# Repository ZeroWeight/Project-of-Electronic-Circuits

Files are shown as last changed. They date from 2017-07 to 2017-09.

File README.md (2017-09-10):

# 电子设计小学期
## 整体工作
- Part 1
    - 在上位机控制下小车完成相关运动
    - 小车安装摄像头，将~~实时~~图像回传给上位机  
- Part 2  
    - 图像回传实时化
    - 小车完成相对位置信息的记录和回传
    - 利用位置信息进行
        - 二维地图的展示
        - 结合图像进行三维重建
- Part 3
    - 应用部署到移动平台
    - 小车安装避障自动运行

## TODOs（完成注明完成者）
- [x] 小车硬件部分 *ZeroWeight@20170830*
    - [x] 电源模块3V3，5，Webench上的开发工作 *ZeroWeight@20170823*
    - [x] PCB *ZeroWeight@20170823*
        - [x] ~~待校验~~ ~~有的焊盘不是特别稳定，需要不断调整~~不是不稳定，需要高级的焊接一发SMT *ZeroWeight@20170901*
    - [x] bts驱动调整 *ZeroWeight@20170830*
    - [x] 舵机调整，测试 *Archer@20170808*
    - [x] IMU，码盘等传感器安装和调试 *ZeroWeight@20170829*
- [x] FPGA部分（包含可能采用myRIO代替的工作） *Archer@20170905*
    - [x] 蓝牙信道的测试
        - 基于HC-05蓝牙转串口模块与上位机通信 ~~，有误码现象，需改进~~。*Archer@20170731*
    - [x] OV7670初始化和数据读取
        - `commit 9108e93` VCC3.3，SCL和SDA接4.7k上拉电阻，输出速度受串口限制。*Archer@20170804*
    - [x] IMU，码盘信息的采集和处理（可能使用myRIO主控） *ZeroWeight@20170905*
- [x] 上位机部分（包含可能的移动平台部署）*ZeroWeight@20170829*
    - [x] 蓝牙信道的测试
        - HC-05模块已设置为slave模式，上位机通过蓝牙连接后使用串口助手即可双向通信。*Archer@20170731*
    - [x] UI开发，整体架构 *ZeroWeight@20170805*
    - ~~[ ] 3D recon的处理~~
    - ~~[ ] 移动平台的部署~~
- [ ] 报告
    - [x] 预习报告 *ZeroWeight@20170827*
        - [x] 选题背景及课题简介 *ZeroWeight@20170825*
        - [x] 方案比较与选择（参考文献评述）*ZeroWeight@20170825*
        - [x] 基于FPGA的数字系统框图 *Archer@20170825*
        - [x] 传感器/执行机构接口电路图 *ZeroWeight@20170827*
        - [x] 基于Webench的电源电路仿真 *ZeroWeight@20170825*
    - [x] 选题展示PPT *Archer@20170827*
    - [x] 总结报告 *ZeroWeight@20170910*
        - [x] 课题开发与调试中出现的问题分析 *Archer&Zeroweight@20170909*
        - [x] 创新点（如有）*Archer&ZeroWeight@20170910*
        - [x] 附完整源码*ZeroWeight@20170909*
        - [x] 工作日志*ZeroWeight@20170909*
        - [x] 作品的视频 *Archer@20170908*
    - [x] 最终展示PPT *ZeroWeight@20170907*

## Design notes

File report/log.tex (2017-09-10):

\documentclass[a4paper]{paper}
\usepackage{ctex}
\usepackage{amsmath}
\usepackage{graphicx}
\usepackage{wrapfig}
\usepackage{multicol}
\usepackage{float}
\usepackage[colorlinks,linkcolor=black,anchorcolor=blue,citecolor=blue]{hyperref}
\title{
    \begin{large}电子技术课程设计\end{large}\\
    基于受控无人车的场地探测和3D重建系统\\
    项目详细日志
}
\author{
    张蔚桐\ 2015011493\ 自55\\
    陈　崴\ 2015011481\ 自55
}
\begin {document}
\maketitle

以下是整个项目的开发日志，代码开源托管在\href
{https://github.com/ZeroWeight/Project-of-Electronic-Circuits}{\underline{代码仓库}}上，这
里是开发过程中的commit记录。
其中各字符意义为\begin{itemize}\item [A]dd:增加文件/功能 \item[U]pdate：更新文件/功能 \item [D]elete:
删除文件/功能 \item [R]elease:发布功能进入稳定模式 \end{itemize}这里的项目日志删除了部分文件系统管理
日志，全部的提交记录请参阅\href{https://github.com/ZeroWeight/Project-of-Electronic-Circuits/commits/master}{\underline{提交记录}}\\ 
陈崴: [U] final commit @ Wed Sep 6 12:54:27\\ 
张蔚桐: [D] rm the useless mode @ Wed Sep 6 11:15:22\\ 
张蔚桐: Merge branch 'master' of github.com:ZeroWeight/Project-of-Electronic-Circuits @ Wed Sep 6 09:53:10\\ 
张蔚桐: [D] rm the labview file @ Wed Sep 6 09:09:28\\ 
陈崴: [A] ultrasonic ranging module @ Tue Sep 5 16:04:07\\ 
陈崴: Merge branch 'local' @ Tue Sep 5 14:55:59\\ 
陈崴: [U] not essential changes @ Tue Sep 5 14:55:41\\ 
陈崴: [U] servo and motor pwm @ Mon Sep 4 15:34:16\\ 
线上修改: Update README.md @ Sun Sep 3 19:34:21\\ 
线上修改: Update README.md @ Sun Sep 3 19:33:34\\ 
张蔚桐: [U] update Readme @ Fri Sep 1 08:40:03\\  
张蔚桐: [U] myRIO project resources @ Thu Aug 31 19:11:54\\ 
陈崴: [A] 7-segment nixietube display module @ Thu Aug 31 14:39:27\\  
张蔚桐: [U] now we can watch connan @ Wed Aug 30 12:51:53\\ 
陈崴: Ha. @ Wed Aug 30 12:39:16\\ 
陈崴: [D] debug @ Tue Aug 29 22:59:25\\ 
张蔚桐: [U] update ignore @ Tue Aug 29 00:25:02\\ 
张蔚桐: [U] Gyo finished @ Tue Aug 29 00:21:06\\ 
张蔚桐: [U] 1st day final host machine @ Mon Aug 28 16:51:38\\ 
张蔚桐: [U] release the host machine @ Mon Aug 28 15:26:18\\ 
张蔚桐: [A] add in myRIO ctrler @ Mon Aug 28 11:52:43\\ 
陈崴: [U] preview ppt @ Mon Aug 28 10:51:26\\ 
陈崴: [A] motor module @ Mon Aug 28 10:49:39\\ 
张蔚桐: [U] renew the host machine coder @ Mon Aug 28 09:25:54\\ 
张蔚桐: [U] recomplie the pdf file @ Sun Aug 27 12:36:37\\ 
陈崴: [U] preview ppt @ Sun Aug 27 11:41:34\\ 
陈崴: [U] fix typos @ Sun Aug 27 11:22:09\\  
陈崴: [A] preview ppt @ Sun Aug 27 11:06:43\\  
张蔚桐: [U] refine the preview report @ Sun Aug 27 10:47:07\\ 
线上修改: Update README.md @ Sun Aug 27 10:40:05\\ 
张蔚桐: [U] finish the preview report @ Sun Aug 27 10:37:57\\ 
张蔚桐: [U] typos and syntax errors fixed in preview report @ Fri Aug 25 18:11:54\\ 
陈崴: [U] report - fpga block @ Fri Aug 25 17:16:48\\ 
陈崴: [U] fpga block @ Fri Aug 25 17:15:56\\ 
陈崴: [U] gitignore @ Fri Aug 25 16:12:16\\  
陈崴: [U] report @ Fri Aug 25 16:01:43\\ 
张蔚桐: [U] webench simu finish @ Fri Aug 25 15:53:36\\ 
陈崴: Merge branch 'master' into local @ Fri Aug 25 14:55:42\\ 
陈崴: [A] FPGA block design @ Fri Aug 25 14:55:29\\ 
陈崴: [U] code indention @ Fri Aug 25 14:53:35\\ 
张蔚桐: [U] README“ @ Fri Aug 25 11:58:08\\ 
张蔚桐: [U] finish report 1 2 @ Fri Aug 25 11:56:54\\ 
张蔚桐: [U] report finish part 1 and 2 @ Fri Aug 25 11:45:14\\ 
线上修改: Update README.md @ Fri Aug 25 11:33:52\\ 
张蔚桐: [U] release PCB @ Thu Aug 24 09:17:36\\ 
陈崴: [U] try baudrate 115200 @ Wed Aug 23 22:35:12\\ 
线上修改: [U] Fin some awkward format errors on markdown @ Wed Aug 23 20:59:47\\ 
线上修改: Update README.md @ Wed Aug 23 20:56:35\\ 
线上修改: Update README.md @ Wed Aug 23 20:55:10\\ 
张蔚桐: [U] finish PCB @ Wed Aug 23 20:49:49\\ 
张蔚桐: [version update] static complie with Qt 5.9 @ Sun Aug 13 18:30:50\\ 
线上修改: Delete DesignRuleCheck.bak @ Fri Aug 11 10:39:47\\ 
线上修改: Delete Design Rule Check - PCB1.html @ Fri Aug 11 10:39:33\\ 
张蔚桐: [D] rm @ Thu Aug 10 09:27:49\\ 
张蔚桐: [U] rm the useless change @ Thu Aug 10 09:26:55\\ 
张蔚桐: [D] remove uesless PCB component @ Thu Aug 10 09:20:24\\ 
张蔚桐: [U] fix bugs of baudrate @ Thu Aug 10 09:15:10\\ 
线上修改: [U] servo @ Tue Aug 8 23:07:08\\ 
陈崴: [U] servo @ Tue Aug 8 22:59:28\\ 
陈崴: [A] servo @ Tue Aug 8 22:58:05\\ 
线上修改: [U] protocol - servo @ Tue Aug 8 22:03:54\\ 
张蔚桐: [A] add on protocol @ Tue Aug 8 10:55:48\\ 
张蔚桐: [A] pushbutton remote control finished @ Tue Aug 8 10:45:58\\ 
张蔚桐: [A] keyboard remote control finished @ Tue Aug 8 10:21:06\\ 
张蔚桐: [A] finish the PCB @ Mon Aug 7 21:00:14\\ 
张蔚桐: [U] update pins for OV @ Sun Aug 6 20:49:45\\ 
张蔚桐: [A] simply finish the PCB design @ Sun Aug 6 18:43:45\\ 
张蔚桐: [U] NOTE the host machine is release @ Sat Aug 5 11:59:01\\ 
张蔚桐: [U][R] Release the host machine - NOTICE     - You can run it in release mode     - Err ratio: approx 20%     - 1fps, but delay may exist     - do not care the free time of the seiral port     - NOTICE the command in /utility.cpp, LINE 82 @ Sat Aug 5 11:53:33\\ 
张蔚桐: [U]IMPORTANT UPDATE: fix bugs of host @ Sat Aug 5 11:27:21\\ 
张蔚桐: [U] temp commit with Graphics all white @ Sat Aug 5 11:13:19\\ 
张蔚桐: [U] temp commit with Graphics to fix @ Sat Aug 5 10:58:12\\ 
张蔚桐: [U] Temp update with bugs to fix @ Sat Aug 5 07:47:19\\ 
线上修改: [U] ov7670 @ Fri Aug 4 23:37:03\\ 
张蔚桐: [U] update host computer     - Greatly rely on performance of the computer     - Err ratio using demo: 1%     - Baud Rate: 1382400     - Without openGL or QImage @ Fri Aug 4 21:58:20\\ 
张蔚桐: [U] refine the structure of serial port @ Fri Aug 4 21:40:33\\ 
张蔚桐: [U] IMPORTANT UPDATE     - No data lost     - TODO: readALL()     - TODO: update the GL (or use QImage instead) @ Fri Aug 4 19:58:34\\ 
张蔚桐: [U] a temp commit with lots of bugs to be fixed @ Fri Aug 4 18:44:43\\ 
张蔚桐: [D] remove the baudrate controller @ Fri Aug 4 17:30:32\\ 
陈崴: [U] ov7670 @ Fri Aug 4 14:32:41\\ 
陈崴: [U] ov7670 works well @ Fri Aug 4 14:25:36\\ 
线上修改: [U] fix @ Fri Aug 4 12:56:41\\  
陈崴: Merge branch 'local' @ Fri Aug 4 12:48:31\\ 
陈崴: [U] ov7670 generally works: 修改了一下初始化配置，不一定比原来好，可以进一步测试。现在初始化返回值共517字节。初始化后的几帧可能不太稳定，直接舍弃。 读取图像速度改为100us每字节，需在上位机方面优化。图像可能出现某块状或条状区域数据异常，表现为彩块或彩条。 @ Fri Aug 4 12:30:52\\ 
张蔚桐: [U] update the BOM @ Thu Aug 3 22:03:29\\ 
张蔚桐: [A] resource of PCB all finished @ Thu Aug 3 18:16:16\\ 
陈崴: Merge branch 'master' into local @ Thu Aug 3 18:13:04\\ 
张蔚桐: [bug fixed]     - fix the bug of exit     - refine the method to write to files     - can accept 10ms/640B input     - may rely on the performance of computer     - NOT stable @ Thu Aug 3 16:59:16\\ 
张蔚桐: [U] output to file, BUG: cant exit normally @ Thu Aug 3 12:39:47\\ 
陈崴: [D] x64/Release/UserInterface.exe @ Thu Aug 3 09:41:27\\ 
陈崴: [U] read frame data (simply tested) 	- 摄像头只可初始化一次，若初始化中断或错误或重新初始化，则需要重新上电。所以注释了OV\_INIT.v LINE51。 	- （未测试）目前只处理了QVGA的一帧，即只使用FIFO的一半空间。 	- 目前发给上位机的数据中，前328B为初始化返回值，若初始化成功，则第7字节为0x73，第11字节为0x76，第327字节为0x0D，第328字节为0x0A，其余字节为0x00。 	- （未测试）从第329字节起为图像数据，前320×240×2字节为RGB565数据，最后2字节为0x0D、0x0A。似乎数据仍有错误，需要进一步测试。 	- 目前发送图像数据的逻辑为：当FIFO中写满了一帧QVGA数据，OV\_READ模块按字节传给顶层，两字节间隔10us；顶层每接收到一个字节，立即以波特率115200发给上位机。 @ Thu Aug 3 00:32:17\\  
陈崴: [U] ov7670 initialization @ Wed Aug 2 21:54:40\\ 
张蔚桐: [A] Bill Of Materials @ Wed Aug 2 15:45:23\\  
线上修改: [U] low level indicates success @ Wed Aug 2 15:04:56\\ 
张蔚桐: [U] clear queue when establishing the connect @ Wed Aug 2 09:14:29\\ 
张蔚桐: [U] upper demo @ Wed Aug 2 09:12:25\\  
张蔚桐: [A] release project to .exe @ Tue Aug 1 20:15:35\\ 
陈崴: [U] fix LINE144 @ Tue Aug 1 20:00:55\\ 
张蔚桐: [U] bug fixed and finish the verify of the image @ Tue Aug 1 19:51:46\\ 
线上修改: [U] fix LINE144 @ Tue Aug 1 19:49:58\\ 
张蔚桐: [U] Finish Serial Port connection @ Tue Aug 1 19:08:30\\ 
陈崴: [A] rtl top (untested) 	整合了摄像头初始化、数据读取和串口通信。 	帧数据按每像素先高字节后低字节的顺序发送至上位机，每帧以0x0D 0x0A结束，共320 × 240 × 2 + 2 = 153602字节。 @ Tue Aug 1 18:28:01\\ 
陈崴: [U] ov7670 initial configuration 	QVGA RGB565 @ Tue Aug 1 18:26:17\\ 
陈崴: [A] read frame data (untested) @ Tue Aug 1 15:09:45\\ 
张蔚桐: [U] preview report section 2 finished @ Tue Aug 1 11:00:10\\ 
张蔚桐: [D] remove useless project in circuit/ @ Tue Aug 1 09:00:58\\ 
线上修改:  [A] sccb interface (untested) @ Mon Jul 31 23:16:26\\ 
陈崴: [U] ov7670 initial configuration @ Mon Jul 31 22:30:30\\ 
陈崴: [A] sccb interface (untested) @ Mon Jul 31 21:32:49\\ 
线上修改: [A] uart modules @ Mon Jul 31 20:08:05\\ 
张蔚桐: [D] del some unuseful qss file @ Mon Jul 31 19:47:15\\ 
张蔚桐: [R] UI basically finished @ Mon Jul 31 18:42:03\\ 
陈崴: [U] bluetooth communication @ Mon Jul 31 16:32:17\\ 
陈崴: [A] uart modules 	Verilog串口模块，波特率可调，8数据位，无校验位，1停止位。 	高波特率时有误码现象，需改进。 @ Mon Jul 31 16:14:46\\ 
张蔚桐: [A] user interface @ Mon Jul 31 11:56:44\\ 
张蔚桐: [F] 3v3 sch finished @ Sun Jul 30 19:50:00\\ 
张蔚桐: [A] PCB lib for AD add in, @ Sun Jul 30 19:08:30\\ 
张蔚桐: [U] report tasks @ Sun Jul 30 11:25:30\\ 
张蔚桐: [A] blank task table finished @ Sun Jul 30 11:16:58\\ 
线上修改: Update README.md @ Sun Jul 30 11:09:12\\ 
张蔚桐: [A] Readme @ Sun Jul 30 11:03:05\\ 
张蔚桐: [A] README @ Sun Jul 30 11:01:59\\ 
张蔚桐: [A] CHN datasheet and SCCB code @ Sat Jul 29 15:59:44\\ 
张蔚桐: [A] OV datasheet and summary @ Sat Jul 29 12:05:27\\ 
张蔚桐: Initial commit @ Sun Jul 9 09:31:41\\ 
\end{document}

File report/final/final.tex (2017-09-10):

% compile with xelatex
\documentclass[a4paper]{paper}
\usepackage{amsmath}
\usepackage{ctex}
\usepackage{diagbox}
\usepackage{float}
\usepackage{graphicx}
\usepackage{multirow}
\usepackage{multicol}
\usepackage{rotating}
\usepackage{wrapfig}
\usepackage[colorlinks,linkcolor=black,anchorcolor=blue,citecolor=blue]{hyperref}
\newcommand{\tabincell}[2]{\begin{tabular}{@{}#1@{}}#2\end{tabular}}
\title{
    \begin{large}电子技术课程设计\end{large}\\
    基于受控无人车的场地探测和3D重建系统\\
    终结报告
}
\author{
    张蔚桐\ 2015011493\ 自55\\
    陈　崴\ 2015011481\ 自55
}
\begin{document}
\maketitle
\tableofcontents    
\clearpage
\section{选题背景及课题简介}
根据《智能交通》和《智能家居》的课题方向，我们将选题定位为基于受控无人车的场地探测和3D重建系统。

\begin{wrapfigure}{r}{0pt}
    \centering
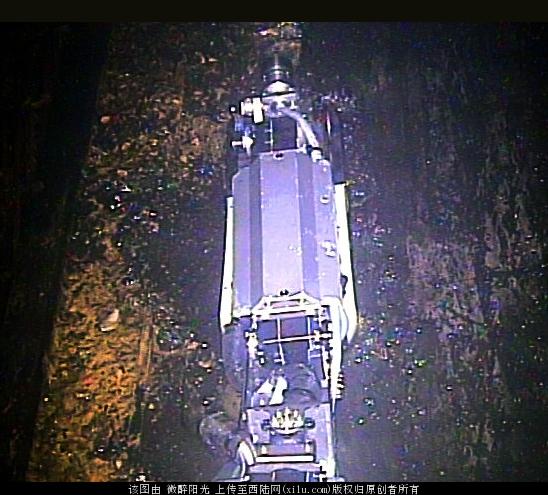
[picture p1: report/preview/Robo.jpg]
    
    \caption{“蝎形”（"scorpion"）机器人行进在福岛核电站2号反应堆内}
    \label{Robo}
\end{wrapfigure}
目前，受控无人车，即对无人车发送指令控制无人车的技术已经有了很多现实生活中的应用。然而，
这种受控无人车要求控制者能够看到无人车的运动状态，并对无人车进行控制。这样不方便无人车进一步
进行无人作业。例如，在地震灾区倒塌的房间中，控制人员无法看到无人车的具体位置，这就需要无人车
对周边环境数据进行采集，方便控制人员进行进一步的控制。另外，通过加装场地检测装置，无人车或
机器人可以到很多危险场合进行作业和信息的采集。例如，2011年日本福岛核泄漏之后，东电公司曾派遣如图
\ref{Robo}所示的机器人到反应堆内调查事故情况。通过加装摄像头和辐射监测设备，机器人可以在人类
无法承受的辐射量内进行高强度监测作业。

另外，目前3D检测和建模技术方兴未艾。利用无人机等设备对建筑物外表面进行3D检测建模的技术已经实现。
计算机视觉领域内，SfM(Shape from Motion)等基于单目摄像机的3D重建技术已经相对比较成熟，因此，
周边技术的成熟为我们的设计提供了相当的基础。同时，我们也考虑采集小车的位置信息，一方面，
对于控制人员来说，了解小车的行进路线（相对位置）也是一个很重要的信息点，另外一方面，根据计算机
的相关知识，我们也可以知道获取准确的拍摄角度和拍摄位置可以更好的加大3D重建的精度，而这方面的应用和算法
据我们所查阅的资料来看相对较少，可以进行进一步的创新。

因此我们将选题定位基于受控无人车的场地探测和3D重建系统，目标是通过控制无人车的行为，完成对场地内
图像信息的采集，并在合适的情况下允许上位机进行3D重建，完成对场景3D状态的描述工作。根据时间限制
和具体的完成情况，我们将整个项目分为如下几个部分进行。
\begin{enumerate}
    \item 第一部分
    \begin{itemize}
        \item 基本的电源管理和小车运动控制
        \item 在上位机控制下小车完成相关运动
        \item 小车安装摄像头，将图像回传上位机
    \end{itemize}
    \item 第二部分
    \begin{itemize}
        \item 图像实时回传
        \item 小车完成相对位置信息的记录和回传
        \item 利用位置信息进行二维地图的展示工作
    \end{itemize}
    \item 第三部分
    \begin{itemize}
        \item 将上位机应用部署到移动平台
        \item 小车安装避障系统，并可以自动运行
        \item 三维重建，同时利用位置信息
    \end{itemize}
\end{enumerate}
从上面我们可以看出整个工程量较大，受到两周的开发时间的限制可能不一定全部完成，剩余工程可以
作为参加挑战杯等进一步开发项目的发展方向。
\subsection{具体完成情况}
这一节总结一下提到的项目内容的完成情况

经过两周的具体调试，我们实现了第一部分的所有具体要求，包括小车的驱动模块，摄像头的安装和
测试，蓝牙模块通信的测试等，并完成了整个项目的整合。但是由于蓝牙速度较慢，经过了长时间的
调试，我们仍然不能实现图像的实时回传，同时，由于图像数据量较大，回传图像对蓝牙压力也比较大
导致蓝牙模块并不是很稳定。虽然如此，整个项目的工作量，完成度和可展示性还是非常理想的，尤其是
对基于FPGA对裸CMOS摄像头OV7670的封装等为代表的工作花费了我们大量的心血，总结起来还是比较满意的。
\section{方案比较与选择}
\subsection{主控元件的选择}
首先我们考虑主控元件的选择，根据我们的技术水平和课题的情况，可供选择的主控芯片为MCU
（单片机）和FPGA。相比FPGA，MCU具有开发相对简单的优势，以串口通信协议为例，大部分MCU
的系统库中均已经封装了串口通信协议，而FPGA相对更接近底层，因此需要自行完成相关的通信协议
的封装，这将消耗大量的时间和精力。

然而，相比于MCU，FPGA在速度和并行性方面有着很大的优势。根据我们查阅的资料，以STMF103为例，
其时钟速度可以达到72MHz，然而由于串行执行的原因，IO速度相对于FPGA较低；对比我们使用的Xilinx
FPGA，其时钟速度可以达到100MHz，同时高度并行使得模块之间互相不干扰，保证了IO速度等要求。

因此，考虑到性能要求以及课程需要，我们在硬件方面采用了FPGA作为主控进行开发。
\subsection{通信机制的选择}
根据查阅的资料，可供选择的无线通信机制有如下三种：

\begin{enumerate}
    \item WiFi信道

    这种通信机制需要将WiFi模块植入硬件，使得小车可以联网传输信息。
    上位机或移动平台使用WiFi下载信息。这种方式的优势一方面是信息传输距离较远，
    在一个路由器覆盖的范围内，信息均可以被传输。另一方面可拓展性也比较强，
    如果设计了合理的联网方式，将进一步解除距离限制，通过将信息上传到云空间，
    用户可以在任何联网的地区完成信息的收取和对小车的控制。

    这种通信机制的缺点是过于复杂，尤其是使用FPGA进行开发的情况下，网络通信协议
    将带来更大的开发时间消耗，不适用于本课程的短期开发。

    \item 蓝牙信道

    这种通信机制利用蓝牙模块，蓝牙模块已经将蓝牙信道封装成串口的形式，
    从很大程度上方便了开发。同时，通过对电脑，移动设备上的蓝牙模块进行开发，
    用户可以不依赖于第三方设备（如路由器）和小车进行通信。虽然通信速度上相比WiFi也
    有一定的损失，并且通信距离受到明显限制，但相比于WiFi模块而言，其功耗更小。

    \item SPI信道

    后期的开发表明，蓝牙的速度并不能保证摄像头传输的实时性，因此后期考虑采用SPI信道
    替代原有的蓝牙信道，然而相比于蓝牙——串口信道，SPI的开发不论是在上位机方面还是在
    FPGA方面均比较复杂，因此不一定可以完成。

\end{enumerate}
综合以上三种通信机制的优缺点，我们选择蓝牙信道作为通信手段。
\subsection{供电方式的选择}
首先通过查阅可能使用到的外设的技术手册，我们大概确定了供电需求为
\begin{itemize}
    \item 5V@1.5A
    \item 3.3V@1.5A
    \item 7.2V@40A
\end{itemize}
其中5V@1.5A负责向FPGA 5V@1A以及舵机供电，3.3V电源负责向外设供电，例如我们采用的摄像头OV7670
采用的供电电压为3.3V@100mA。7.2V@40A电源负责向电机供电，并应接受PWM调制来控制电机转速。

通过查阅资料我们发现，供电的难点在7.2V@40A电源，而5V@1.5A电源和3.3V@1.5A电源
均可以使用实验室提供的TPS54160 SMT芯片完成设计，
这一部分内容将在后面基于Webench的仿真实现上面进行说明。7.2V@40A电源的电流限额主要受到电机供电电流要求
影响，从实验室提供的数据手册我们可以发现，电机的空载电流2.4A，最高效率电流11A，堵转电流52.8A，根据网上
查阅的相关资料，电机的限流应当是最高效率电流的约4倍，因此设计7.2V@40A电源负责向电机供电。

这里讨论7.2V@40A电源的设计问题。因为需要接受PWM信号调制，因此我们采用了H桥进行设计。
\begin{wrapfigure}{r}{0pt}
    \centering
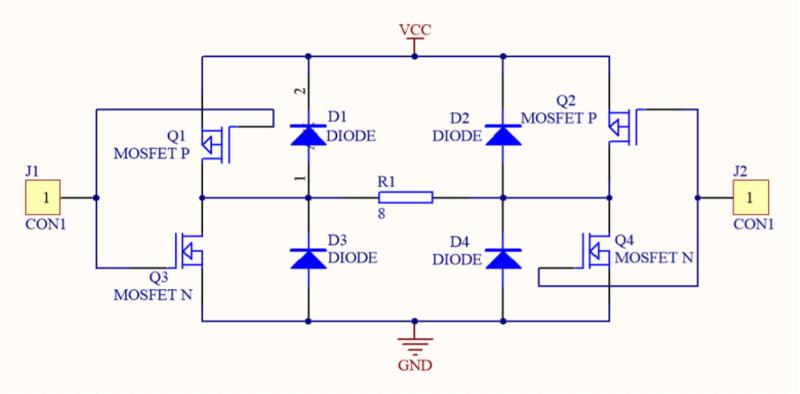
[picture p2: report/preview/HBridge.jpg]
    
    \caption{H桥的电路原理图}
    \label{H-bridge}
\end{wrapfigure}
H桥的电路原理图如图\ref{H-bridge}所示。Q1\~Q4可以由处于饱和状态的三极管或开关状态的MOS管组成 
J1 和 J2 分别接入前一级驱动电路产生的两个反相PWM，设某时刻 J1 为高电平，
则 Q3 导通，Q1 截止；由于反相，J2 为低电平，Q2 导通，Q4 截止，
电流由通过 Q2，经负载，再经过 Q3 流入地。
同理，当某时刻 J1 为低电平时，Q1,Q4 导通， Q2,Q3 截止，
电流依次经 Q1,R1,Q4 流入地。综上，任意时刻有且只有一个对角线上的两个MOS管是导通的。

对于电机，我们可以设定刹车模式，即可以通过与上述方法类似的方法将电机两脚短路，使得电机
迅速产生电磁制动实现刹车效果

通过搜索符合要求的元件，我们发现合理的解决方案为bts7960/7961芯片和自行搭建H桥两种方案。

bts7960/7961芯片是接受5VPWM信号调制的，输入电压5.5V至27V@43A的半H桥电路，
采用SMT封装，输出电流符合要求。
然而，由于我们电机的额定输入电压为7.2V，经过对电机的初步调试我们可以发现
电机在7.2V输入电压下的转速非常高，导致速度不能得到控制，
经过进一步的实验我们发现，在低于数据手册上提供的5.4V供电的情况下，
电机的转速可以保证一个理想的状态，因此可以初步得到结论即PWM信号的占空比不可过高。

而自行搭建H桥，因为工艺比较复杂，同时在网上找不到合适的大功率MOS管供应商，
因此我们放弃了这个方案。

\subsection{摄像头数据传输技术的选择}
我们采用的OV7670摄像头，可以输出25fps 640*480 VGA格式的RGB三色图像，输出采用8线同步并行传送
因此输出时钟速度可以达到$25*640*480 \approx 8\mathrm{MHz}$。
收到蓝牙信道是串行接口的原因，蓝牙信道的速度必须达到8MB/s，这是一般蓝牙系统很难做到的。
因此不论是FPGA读取信息还是蓝牙传输信息的速度，均不如摄像头采集数据的速度，需要找到合理的解决方式。

经过我们查阅相关资料发现，OV7670的传输方式有如下三种形式：
\begin{wrapfigure}{r}{0pt}
        \centering
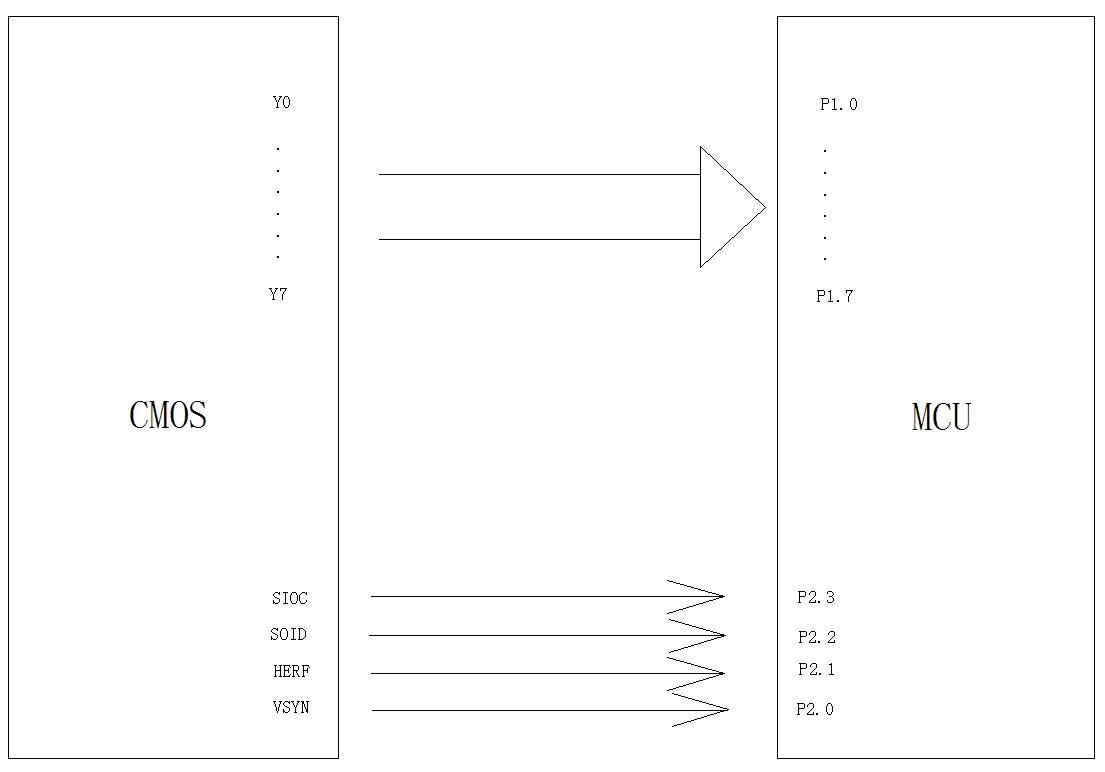
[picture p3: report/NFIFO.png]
        
        \caption{MCU/FPGA直接采集}
        \label{fig2}
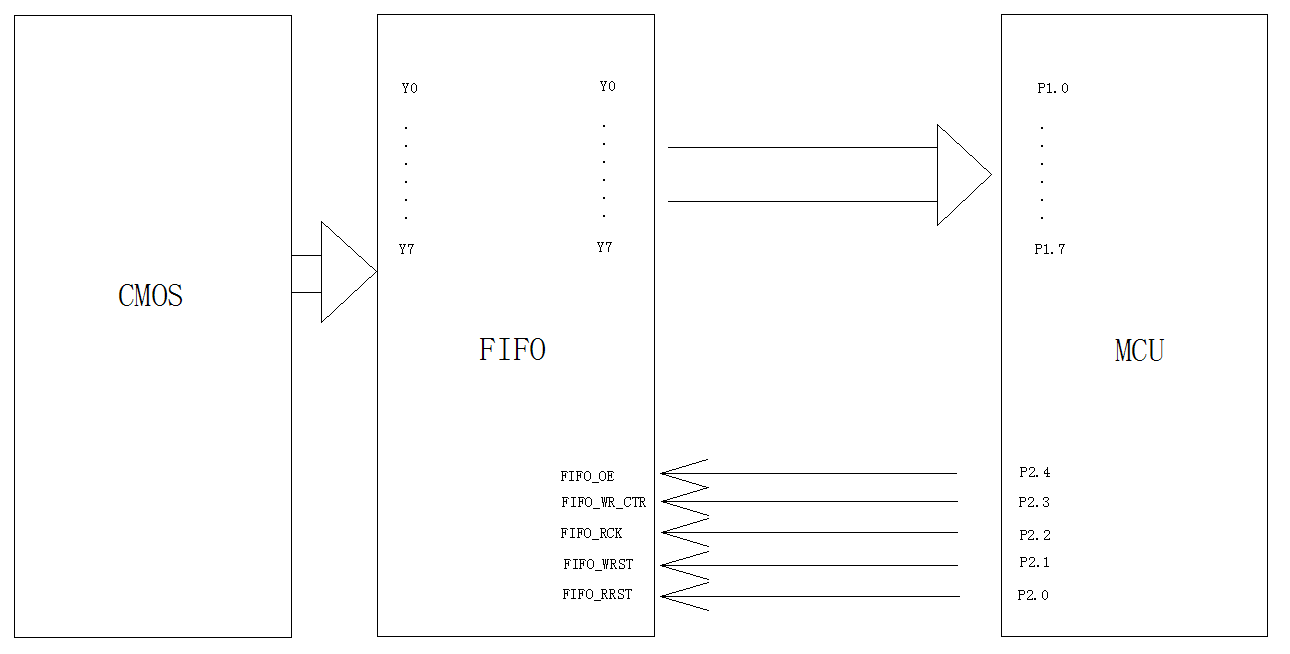
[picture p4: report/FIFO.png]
        
        \caption{FIFO采集}
        \label{fig3}
\end{wrapfigure}
\begin{itemize}
    \item MCU/FPGA直接采集：

    如图\ref{fig2}所示，这种方法是最简单，最直接，但也是最不好实现的方法，
    以MCU为例，多数的CMOS 芯片（如OV7670）的时钟速度可高达24M，
    一般MCU的IO 端口速度根本不可能达到，所以需要高速MCU。
    这对多数用户来讲有些不现实。但也不是完全没有办法在低速上实现采集，
    方法也很简单，那么就是降低CMOS的输出速度，
    不过这需要靠外部的晶振和内部的PLL电路以及像素时钟速度，
    帧速等多个寄存器共同设置，并且要和MCU的IO速度匹配才可实现。
    但这么做将带来巨大的寄存器设置工作量并导致硬件图像的采集速度
    可能下降到0.5帧以下，同时带来图像失真的可能。
\end{itemize} 

\begin{itemize}
    \item DMA方式

    这种方式主要用于MCU中，FPGA中这种方式效果不明显，DMA控制器使得数据
    可以绕过CPU直接进入内存，但是在FPGA中，同时受到串口通信速度的影响，
    这种方式效果也不是很明显。

    \item FIFO模块采集

    如图\ref{fig3}，用户只需要按上述时序图控制相关的几个控制引脚即可，可以很
    方便的使用在低速MCU上，另外一个好处是，可以直接IO口读取数据，
    读出的数据可以直接送屏，也可以经过MCU简单处理；当然也可以不经过
    MCU，直接送到屏等外围器件使用。对于FPGA，以及速度相对较低的串口单元，
    使用FIFO也能很大程度的解决速度不同步的问题。

\end{itemize}
\subsection{车辆位置角度信息处理方式的选择}
为了进一步增强3D建模的精度，我们希望能够采集车辆的位置信息和角度信息。
由于摄像头和车辆是相对固定的，这样也就获得了摄像头的位置信息和角度信息。

根据我们查阅到的资料，车辆的位置信息和角度信息有几种不同的获取方式，如下所示。
\begin{itemize}
    \item 惯性测量单元（IMU）模块

    通过加速度计和陀螺仪的信息，可以直接读取车辆的加速度和角度。
    经过积分之后可以得到车辆的速度信息和角度信息，这种方法最简单，
    但是误差最大，加速度计易受到颠簸，碰撞，刹车等造成的脉冲影响，
    并进一步影响积分的准确性。角速度计（陀螺仪）具有一般性的零点迁移
    问题，这包括动态的零点波动和静态的温漂。经过积分会导致角度信息
    相当不准确。这种方法只能作为一种简单的参考，实用时必须加以处理。

    \item 磁场计

    通过对地磁角度的测定，可以直接获取车辆的角度，并通过加速度计等
    方式获得车辆的速度，这种方式误差相对前一种较小，
    但是受外界磁场的影响比较严重，尤其是当存在10A绕组的电机驱动时，
    这种方法可以认为无效。

    \item 码盘

    这种方法通过测量车辆四轮的转速经过解算得到车辆的具体位置，相比于
    之前几种方式，这种方式依赖于更加准确的光电传感器，因此得到的值也
    相对比较准确，这种方法的难点在于必须对车辆的刚性模型进行建模，
    同时安装码盘也是一个硬件上的难点。
\end{itemize}
综合提到的几种方法，我们计划采取IMU+信号处理+码盘解算几种方式
得到车辆的具体位置，希望通过反馈等方式希望得到更准确的车辆控制。

\subsection{其他注意事项}
在设计对车辆相对位置进行测量的过程中，考虑到FPGA在解算浮点数方面比较难以开发，
我们选用了NI myRIO进行解算和控制，并采用myRIO自带的WiFi进行相关数据的回传。

NI myRIO是NI针对教学和学生创新应用而最新推出的嵌入式系统开发平台。
NI myRIO内嵌Xilinx Zynq芯片，使学生可以利用双核ARM Cortex-A9的
实时性能以及Xilinx FPGA可定制化I/O，学习从简单嵌入式系统开发到
具有一定复杂度的系统设计，采用LabView语言进行可视化编程。
通过myRIO可以大幅简化控制算法如PID的调试过程，显著降低开发难度，加速开发进度。
\subsection{实际项目的修正和改动}
实际项目进行过程中，我们尽可能的对蓝牙的速度进行了利用，然而由于蓝牙速度受限，
导致实际上图像回传不能实时化，并且对蓝牙通信速度上限的冲击导致蓝牙出现不稳定情况。
在这种情况下，我们希望采用SPI-WiFi-TCP通信协议，然而TCP协议封装复杂，
经过我们查阅相关资料，TCP的引脚数量甚至超过了我们使用的FPGA的全部可控引脚数量，‘
同时TCP通信机制也比较复杂，会对是FPGA层面的封装还是上位机的编写带来巨大的困难，
因此我们最终放弃了这种思路。

同时，对于陀螺仪和测速方面，由于我们使用的FPGA引脚已经全部被占用，导致基于FPGA
的相关开发变得不现实，因此我们选用了NI myRIO进行相关的开发，并完成了陀螺仪模块。
对于测速模块，我们发现不论是车轮还是电机均很难安装码盘，因此我们采用了对车轮进行
标注并利用红外进行测速，并基于myRIO调通了相关的功能，然而由于我们设计的车辆行驶
速度偏慢，因此相关的测速变得没有实际意义，最终我们放弃了这个模块的整合工作。
\section{基于FPGA的数字系统框图}
\begin{figure}
    \centering
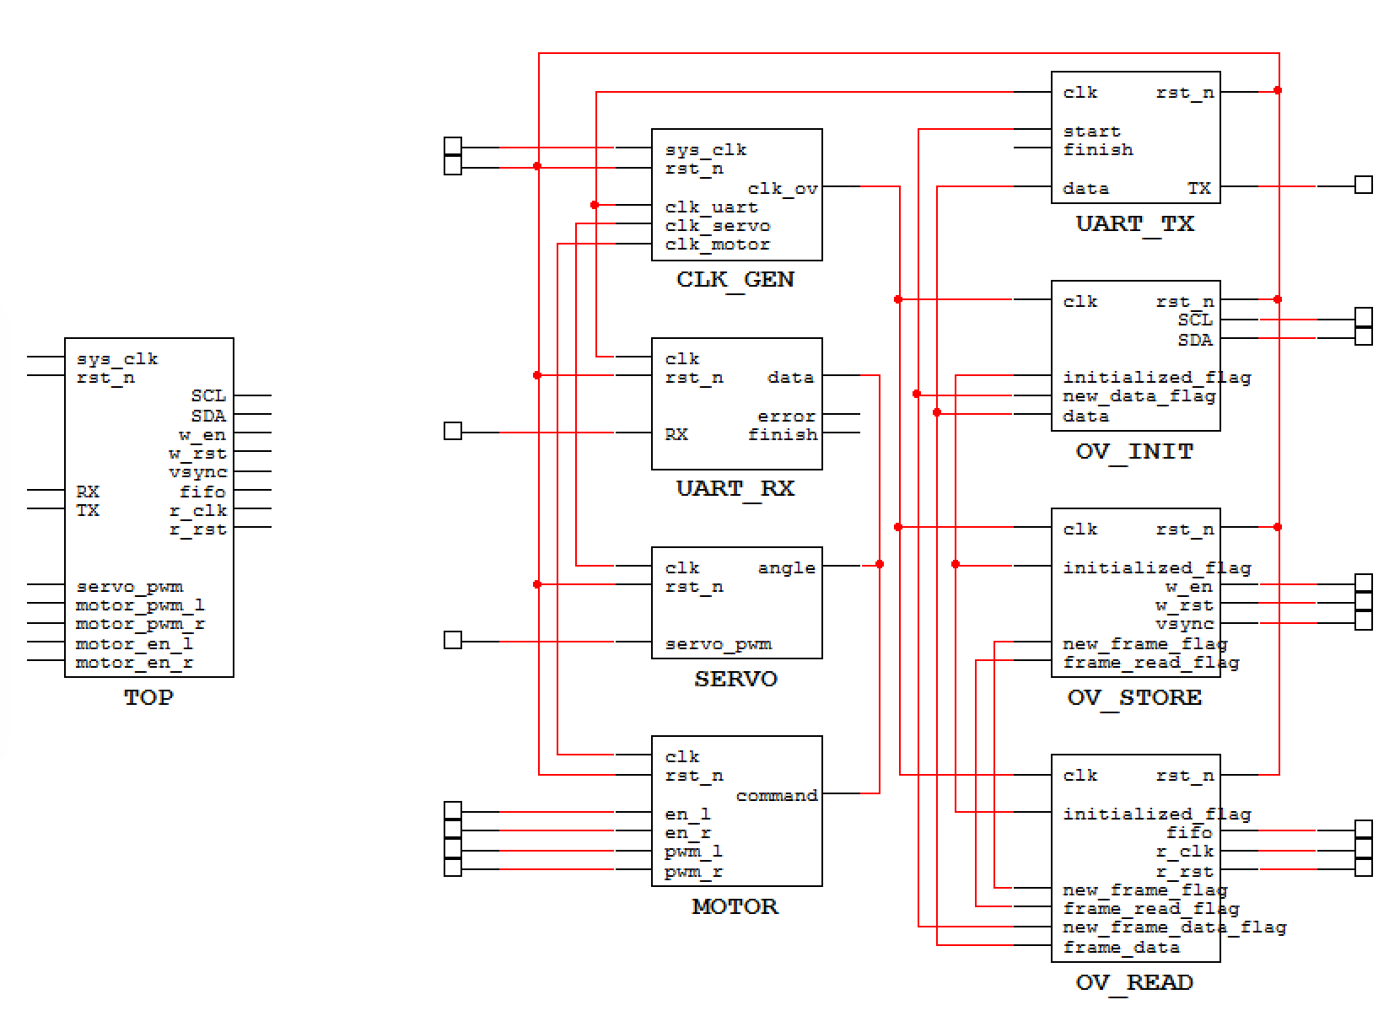
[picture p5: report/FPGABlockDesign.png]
    
    \caption{基于FPGA的数字系统框图}
    \label{FPGABlockDesign}
\end{figure}
如图\ref{FPGABlockDesign}所示，左侧为封装的顶层模块，从右侧可以看出共分为8个子模块。
\begin{itemize}
    \item CLK\_GEN

    该模块对100MHz系统时钟分频，输出4个时钟分别供串口、舵机、电机、摄像头使用。

    \item UART\_RX

    蓝牙串口接收模块，RX为数据线，每从上位机接收一个码元即触发finish信号，并将数据存
    在data寄存器供其他模块使用。同时内部还提供了一个error接口，接收数据发生错误时触发。

    \item UART\_TX

    蓝牙串口发送模块，TX为数据线，当触发start信号后，将data寄存器中的内容发送给上位机，
    发送完成后会得到一个finish信号反馈。

    \item SERVO

    舵机控制模块，从串口接收转向控制指令，输出舵机PWM信号。

    \item MOTOR

    电机控制模块，同样从串口接收指令，输出电机使能和PWM信号。

    \item OV\_INIT

    摄像头初始化模块，SCL和SDA为SCCB协议的时钟线和数据线，初始化前initialized\_flag为
    低电平，OV\_STORE和OV\_READ处于失能状态，初始化完成后拉高initialized\_flag，摄像头
    便可正常工作。

    \item OV\_STORE

    将摄像头采集到的图像存储于FIFO中，存储完成一帧后触发new\_frame\_flag信号，等待FPGA
    读取图像结束后才继续采集下一帧。

    \item OV\_READ

    从FIFO中读取一帧图像，并存储在frame\_data寄存器中，读取完成后触发两个信号，一个是
    frame\_read\_flag，通知摄像头可以继续采集下一帧图像，另一个是new\_frame\_data\_flag，
    通知顶层模块将读取到的数据发送给上位机。
    
\end{itemize}
\section{传感器/执行机构接口电路图}
\subsection{传感器电路}
\subsubsection{数字接口电路}
\begin{wrapfigure}{r}{0pt}
    \centering
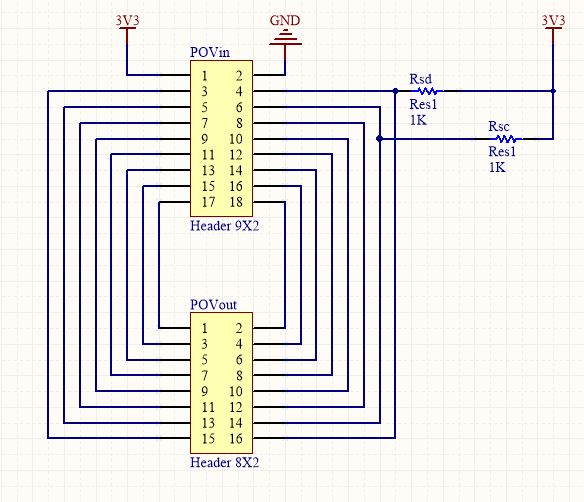
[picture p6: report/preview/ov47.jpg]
    
    \caption{OV上拉电阻和转接电路}
    \label{OV}
\end{wrapfigure}
这部分主要是完成数字模块之间的接口电路，由于各个数字模块已经将输出电平统一标准化为TTL电平，
因此这部分的关键主要是接口通信协议的实现，主要有FPGA方面实现了SCCB接口通信协议，串口通信协议，
摄像头数据读取协议等。另外，SIO\_C和SIO\_D分别为SCCB总线的时钟线和数据线，为了
方面对多个设备进行控制，OV的SCCB两个端口采用的均是OC门输出，需要上拉4.7k
电阻实现输出高低电平，这些需要在设计PCB的时候尽可能的考虑到并保证接线的
稳定性和摄像头位置的稳定性，因此需要在PCB上统一制作并提供对FPGA的简单的接线电路，这部分的电路
可以如图\ref{OV}所示。

\begin{wrapfigure}{r}{0pt}
    \centering
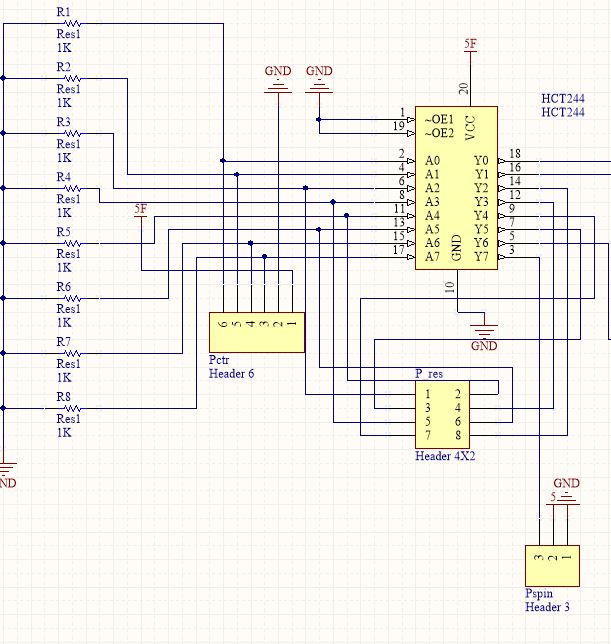
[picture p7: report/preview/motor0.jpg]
    
    \caption{74HC244驱动器电路}
    \label{motor0}
\end{wrapfigure}
另一部分的接口电路问题是3.3V电平标准和5V电平不匹配的问题以及同时设计到的FPGA驱动能力不足的问题
通过查阅给定的技术手册我们发现FPGA输入电流1A，标准的输出电压为3.3V，
而不论是电机驱动的PWM还是舵机驱动的PWM均为5V，这中间需要设计适当的接口
电路，同时，由于工程量比较大，担心FPGA会出现总线电流过大或无法驱动相关
接口电路的情况，因此我们采用了74HC244芯片作为接口的辅助电路，74HC244是
一款高速CMOS驱动芯片，支持三态门使能，通过HC244我们可以顺利的将3.3V输出转化为5V，
并提升驱动能力。根据74HC244的接线要求，我们在输入端接入下拉电阻1k实现相关功能。这部分的电路
有如图\ref{motor0}所示。同时我们将剩下的74HC244引脚同样通过排针引出，留待之后使用。

\subsubsection{模拟接口电路}
\begin{wrapfigure}{r}{0pt}
    \centering
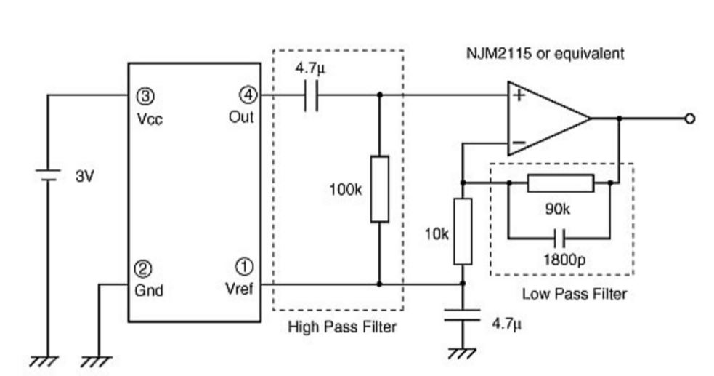
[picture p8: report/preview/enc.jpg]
    
    \caption{ENC-03模块外部电路图}
    \label{ENC}
\end{wrapfigure}
我们计划采用输出模拟电压的ENC-03陀螺仪，这是是一种应用科氏力原理的角速度传感器，
陀螺输出一个和角速度成正比的模拟电压信号。通过积分电路可以得到相关的角度等。根据ENC-03
技术手册，我们设计输出放大电路如图\ref{ENC}所示，整个电路由两个滤波器组成，左侧为低通滤波器，
用于滤除传感器高频噪声，右侧为高通滤波-放大电路，用于放大电压信号和滤除低频温漂。

进一步，我们搭建基本积分电路可以得到角度信息，两个信息通过AD模块可以返回给主控设备。
由于我们计划采用myRIO进行位置信息的测量，因此这部分可以直接使用LabVIEW语言在myRIO上完成，
就没有设计电路的必要了。

\subsection{执行接口电路}
这部分主要描述的是对电机和舵机的驱动电路

对于舵机驱动，单片机输出高电平为3.3V的PWM脉冲，经过前文提到过的74HC模块转5V驱动舵机旋转。

\begin{wrapfigure}{r}{0pt}
    \centering
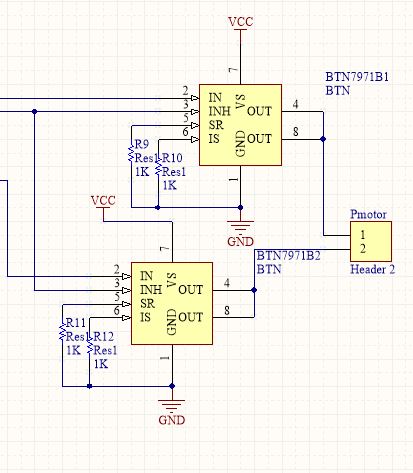
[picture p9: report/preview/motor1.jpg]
    
    \caption{电机驱动电路}
    \label{motor1}
\end{wrapfigure}
对于电机驱动，我们使用BTN7970模块，如图\ref{motor1}所示。这里为了方便后文叙述，两片IN引脚被
命名为IN1，IN2，两片INT引脚被命名为INT1,INT2。我们将INT1,INT2短接并输入PWM波形控制电机转动速度。
将IN1，IN2分别接高低电平控制电机正转反转。例如\{INT1 = 0,INT2 = 1\}代表电机正转，\{INT1 = 1,
INT2 = 0\}代表电机反转。当\{INT1 = 0,INT2 = 0\}时，H桥全部关断，表示不控制电机转动。
当\{INT1 = 1,INT2 = 1\}时，H桥下部导通，电机两端短接，使得电机的机械能通过电磁感应和短路线
迅速释放，实现刹车功能。BTN相关引脚仍为5V接线，因此使用74HC244完成相关的电平转换和放大工作。
\section{基于Webench的电源电路仿真}
WEBENCH是TI公司提供的设计环境，通过软件工具提供定制电源等的设计，通过使用WEBENCH可以
提升设计效率。整体的设计思路如下：
\begin{itemize}
    \item 输入电压的确定

    我们将电池断开，测量电压约为8.2V，将电池直接接电机，并在电机上施加比较大的阻力，发现
    电源电压约为7V，因此我们设计电源时考虑输入电压为6V\~9V即可满足需求。

    \item 输出电压的确定

    由表\ref{t1}所示，我们需要向FPGA提供5V外接电源，对舵机提供5V外接电源，
    对外设提供3.3V外接电源，因此设计输出电压为5V，3.3V。

    \item 输出电流的确定

    首先根据实验室提供的TI样片，我们选择了TI TPS54160降压模块，TPS54160器件是一款带有集成型
    高侧MOSFET的60V,1.5A的降压稳压器。电流模式控制提供了简单外部补偿和灵活组件选择，功耗较小。

    根据TPS54160的输出电流，我们限制电源输出电流为1.5A。同时查阅技术手册可以得到主要的部件
    的供电信息如表\ref{t1}所示,总计需要输出电流5V@2A,3.3V@500mA，因此需要设计两路5V供电电源，
    其中一路FPGA自用（包括驱动器74HC244），一路给舵机/外设使用。

\end{itemize}
因此，进入WEBENCH中提供需求的输入，输出信息，选择器件为TPS54160，可以得到元件的原理图。
通过调整原理图上的元件的值的信息，可以选用已有阻值的元件进行仿真，最终确定的电路原理图和
响应时间仿真和稳态仿真如下面几张图所示。两个电路结构相同，相关参数差别如表\ref{t2}所示。
整理仿真结果如表\ref{t3}所示。可以看出电源的性能效果还是比较理想的，可以进行实际电路的搭建。
\begin{figure}
    \centering
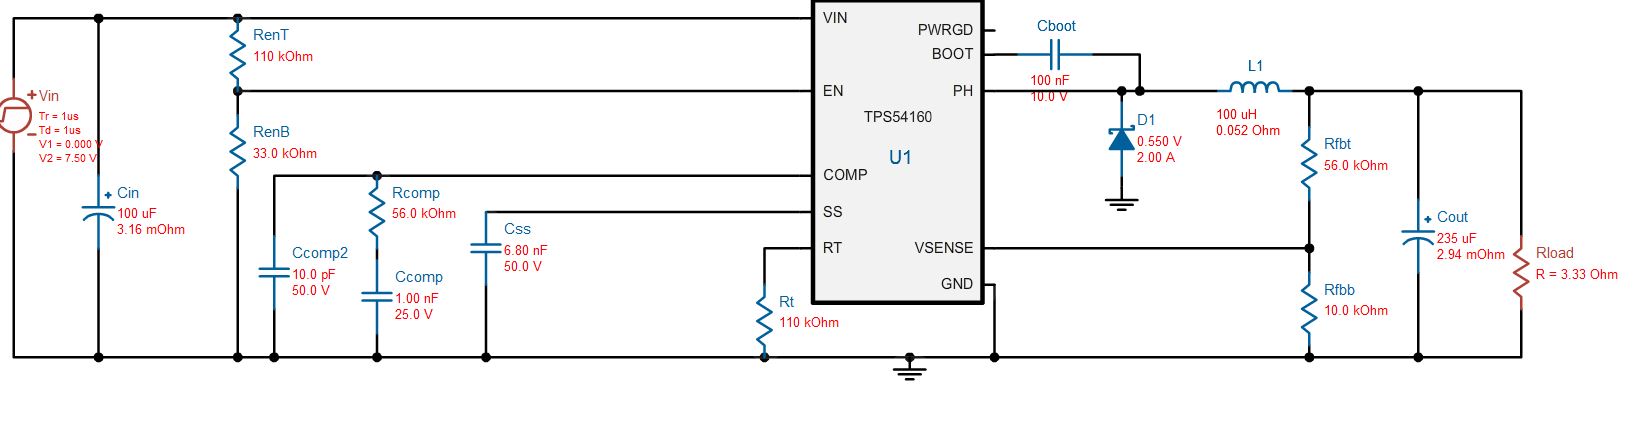
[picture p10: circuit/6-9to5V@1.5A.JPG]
    
\end{figure}
\begin{multicols}{2}
    \begin{table}[H]
        \centering
        \caption{主要部件供电信息}
        \label{t1}
        \begin{tabular}{|c|c|c|} \hline
            部件& 电压& 电流\\ \hline
            FPGA& 5V& 1A \\ \hline
            舵机& 5V & 800mA \\ \hline
            74HC244 & 5V& 100mA\\ \hline
            蓝牙模块 & 5V& 100mA\\ \hline
            OV7670& 3.3V& 200mA \\ \hline
        \end{tabular}
    \end{table}
    \begin{table}[H]
        \centering
        \caption{仿真主要性能指标}
        \label{t3}
        \begin{tabular}{|c|c|c|} \hline
            参数&3.3V电源&5V电源\\ \hline
            稳态电压平均值& 3.435V&5.326V\\ \hline
            稳态电压峰峰值& 3.648mV &2.465mV\\ \hline
            启动时间& 1.368ms&2.379ms\\ \hline
            电感电流峰值& 1.245A&1.753A\\ \hline
        \end{tabular}
    \end{table}
\end{multicols}
\clearpage
\begin{table}
    \centering
    \caption{元件参数信息}
    \label{t2}
    \begin{tabular}{|c|c|c|c|} \hline
        元件名&类别/单位& 3.3V电源& 5V电源\\ \hline
        Cin&电解电容/$\mu$F&470&470\\ \hline
        Rent&定值电阻/k$\Omega$&110&110\\ \hline
        RenB&定值电阻/k$\Omega$&33&33\\ \hline
        Ccomp&独石电容/nF&1&1\\ \hline
        Ccomp2&独石电容/pF&10&10\\ \hline
        Rcomp&定值电阻/k$\Omega$&33&56\\ \hline
        Css&独石电容/nF&6.8&6.8\\ \hline
        Rt&定值电阻/k$\Omega$&110&110\\ \hline
        Cboot&独石电容/nF&100&100\\ \hline
        D1&肖特基二极管/型号&SS24FL&SS24FL\\ \hline
        L1&定值电感/$\mu$H&100&100\\ \hline
        Rfbt&定值电阻/k$\Omega$&33&56\\ \hline
        Rfbb&定值电阻/k$\Omega$&10&10\\ \hline
        Cout&电解电容/$\mu$F&470&470\\ \hline
    \end{tabular}
\end{table}
\begin{multicols}{2}
    \begin{figure}[H]
        \centering
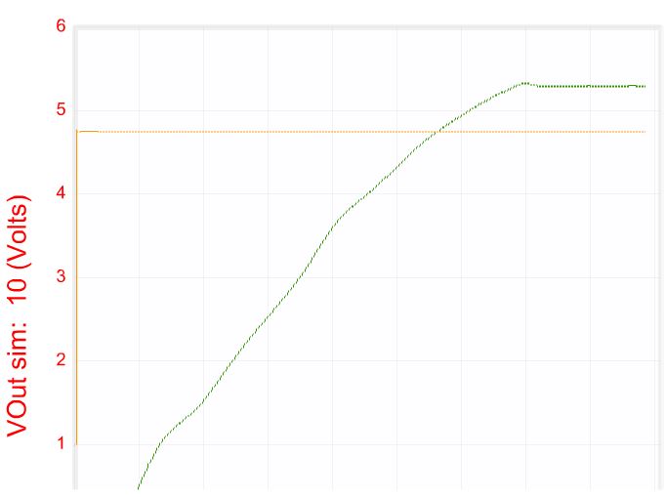
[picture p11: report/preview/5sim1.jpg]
        
        \caption{5V电源启动情况}
    \end{figure}
    \begin{figure}[H]
        \centering
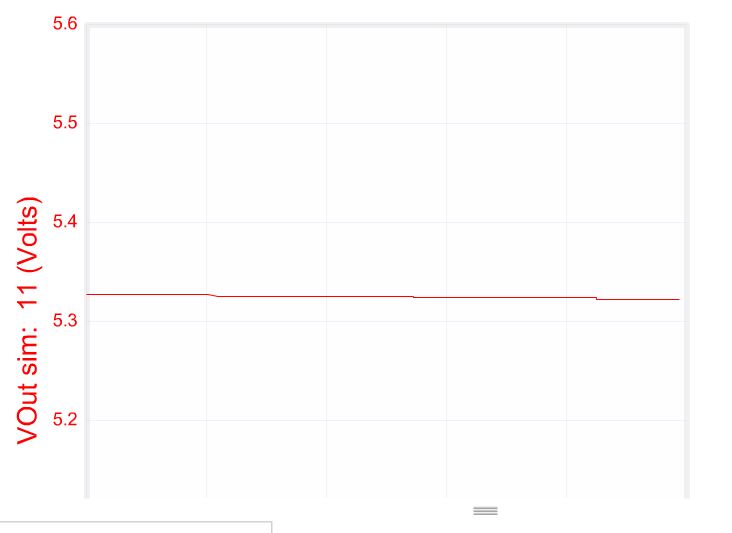
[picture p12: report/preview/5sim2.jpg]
        
        \caption{5V电源稳态情况}
    \end{figure}
    \begin{figure}[H]
        \centering
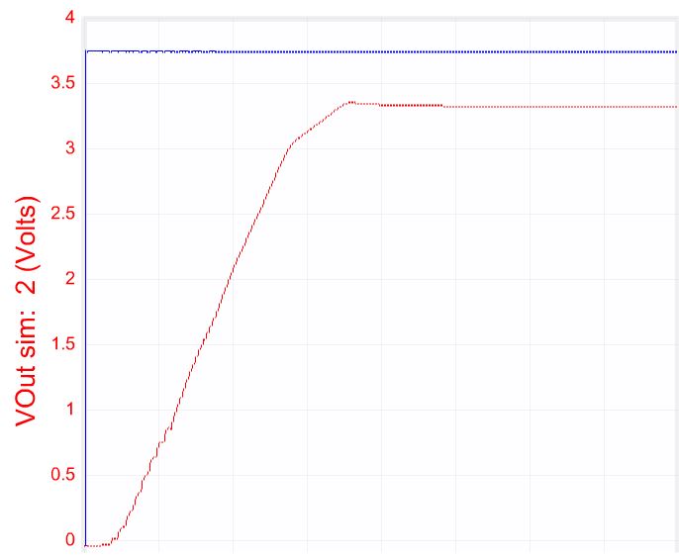
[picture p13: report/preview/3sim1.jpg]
        
        \caption{3.3V电源启动情况}
    \end{figure}
    \begin{figure}[H]
        \centering
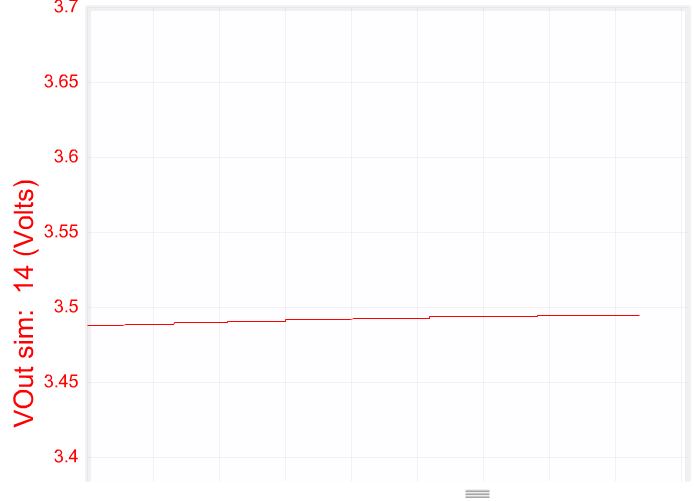
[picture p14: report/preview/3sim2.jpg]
        
        \caption{3.3V电源稳态情况}
    \end{figure}
\end{multicols}
\section{PCB的设计制作}
完成了电源模块的仿真之后就可以开始着手进行PCB的设计制作了，在设计制作的过程中，由于考虑到
手工焊接的困难，因此尽可能多的选用了插接件代替SMT封装元件，如电阻，电容等，同时，根据走线可能
涉及的电流大小如图\ref{fig4}所示，我们设计走线宽度为
\begin{itemize}
    \item 对BTN驱动板，走线40mil(1mm)，对应电流3A左右
    \item 对电源管理模块，走线15mil(0.4mm)，引脚处走线10mil(0.25mm)，对应电流1.5A左右
\end{itemize}
同时对大电流部分加焊锡保护走线，防止过热。整版PCB单面布线，背面加装散热片，保证散热顺畅并注意
IC散热引脚接触良好。同时考虑接线端子，IC等的位置关系，充分考虑日后安装，打孔位置，
保证接线顺利同时散热合理。PCB如图\ref{pcb}所示。
\begin{table}
    \centering
    \caption{PCB线宽和电流的关系}
    \label{fig4}
    \begin{tabular}{|c|c|c|c|c|c|} \hline
        电流(A)&线宽(mm)&电流(A)&线宽(mm)\\ \hline
        6.0&2.5&5.1&2.0\\ \hline
        4.2&1.5&3.6&1.2\\ \hline
        3.3&1.0&2.8&0.8\\ \hline
        2.3&0.6&2&0.5\\ \hline
        1.7&0.4&1.3&0.3\\ \hline
        0.9&0.2&0.7&0.15\\ \hline
    \end{tabular}
\end{table}
\begin{figure}
    \centering
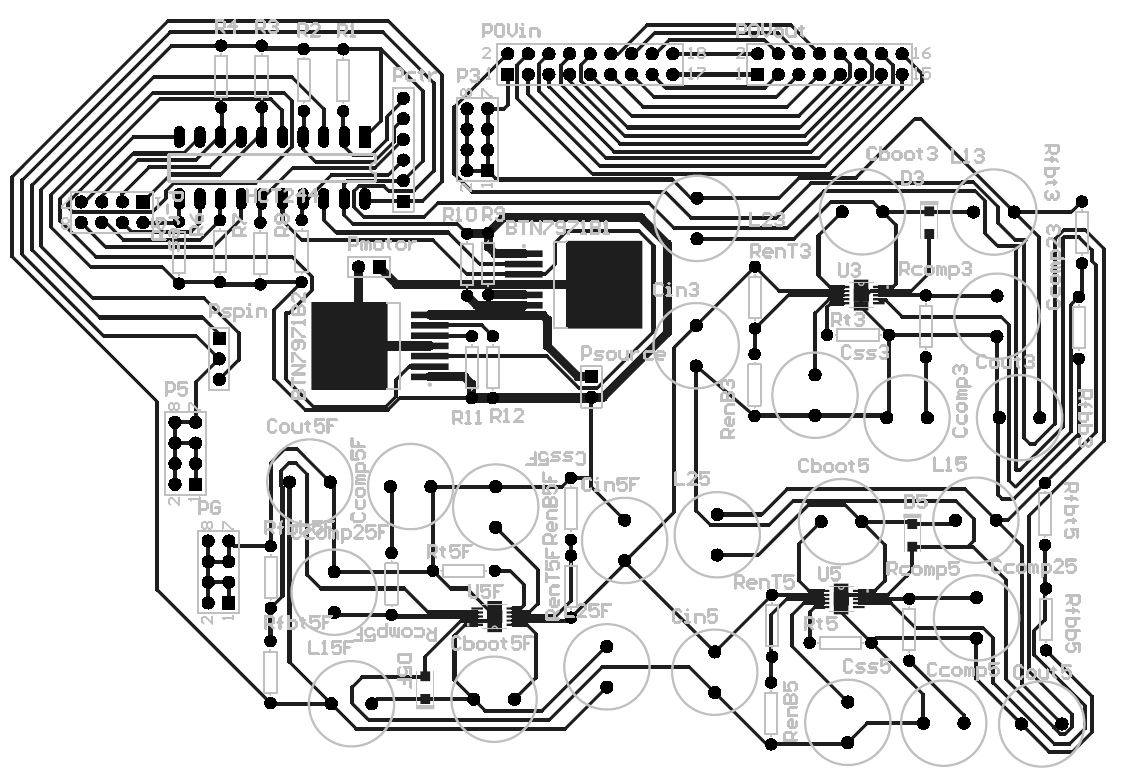
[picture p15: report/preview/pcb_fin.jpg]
    
    \caption{PCB版效果图}
    \label{pcb}
\end{figure}
\section{课题开发与调试中出现的问题分析}
\subsection{数字电路部分}
数电部分完全使用FPGA进行开发，遇到的困难几乎都来自ov7670图像传感器模块。

首先，图像传感器在工作前需要先进行寄存器初始化配置，读写寄存器使用的是SCCB协议。一开始调试时，
待写入的寄存器的地址和内容都存放在文本文件中，且因为数据是串行写入，各个寄存器的初始化是顺序
执行的，所以初始化语句都写在initial块中，又由于每次读或写一个寄存器都需要SCCB协议中的起始、
应答、结束等信号，这就会产生大量对时钟线重复的操作，为了使代码看起来更简洁，这些相同的操作都
封装成了task。这样一来，尽管在仿真测试时代码都正常运行，但电路却是不可综合的。

最后，解决这些问题的方式是重写代码，将各寄存器地址和内容都以常量形式存在FPGA中，以FSM状态的
跳转模拟各语句的顺序执行，大量相同的操作也只能重复相同的代码。其中还发现寄存器配置需要一定的
反应时间，因此每写入一字节后都加入几毫秒的延时。

图像传感器的初始化只进行一次，而图像的采集和读取是无限循环的，且必须在初始化完成后才能进行，
所以使用了一个全局的信号来判断初始化是否完成。前文已经分析过使用FIFO模块采集图像的好处，
但是在我们查阅到的资料中，绝大部分不带FIFO的传感器封装成18个引脚，带FIFO的传感器封装成22个
引脚，而为了节省FPGA的IO，我们选购的传感器是带FIFO模块且封装为18个引脚的，这种封装的资料
几乎找不到，开发完全没有前车之鉴，只能依赖于ov公司和FIFO芯片的数据手册。这些数据手册中提供的
都是各IC引脚的时序，而封装后外部引脚的时序只能靠分析和推测。在硬件调试时，我们合理地使用FPGA上
的LED进行辅助调试，通过LED的状态来分析电路状态，从而找出代码中的错误，大大节省了开发时间。

通过蓝牙串口模块回传数据时，理论上传输速率可以达到1.3秒每帧，但实际测试中发现，如果以这么高的速率
发送数据，蓝牙模块的数据吞吐量已经达到极限，会发生误码、丢包、甚至蓝牙连接中断的现象。受硬件
性能所限，只能在传输一字节后加入至少100us的延时间隔，使蓝牙模块能够较稳定地工作，最终展示时，需要
采用串口替代蓝牙来加速传输速度。
\subsection{模拟电路部分}
模拟电路部分主要包括电源驱动模块和电机驱动模块问题，虽然通过查阅技术手册和基于WEBENCH的仿真可以看
到基本的电路，但是从电路原理图到电路实际工作还有很远的距离。

首先是电路原理图的设计，通过查阅资料，我们发现实验室提供的TPS54160模块输出电流为1.5A，设计的5V电
源不能很好的驱动FPGA（1A）和舵机（800mA堵转）。因此我们设计FPGA和PCB上的其他元件一路供电，舵机和
其他外设一路供电。这种设计虽然降低了电路的负载，但是显然不可避免地增加了电路的规模和后续布线，制
版，焊接的压力。

我们将整个电路进行整合为一块PCB，这样从最大程度上减少了可能存在的飞线和不稳定的情况，然而过大体量
的电路带来了布线，制版，焊接的困难。使用AD模块制作PCB的过程中，首先遇到的问题是AD不能提供我们需要
的元件封装库，因此我们参照元件的技术手册自行设计了封装图。其次，包括74HC244模块等模块以及电阻电容
等存在贴片（包括SOP，SSOP封装）以及插接封装（包括DIP封装），经过无数次的布线尝试，我们尽可能的选
择插接件来降低后续布线，焊接的难度。

接下来的布线部分，首先遇到的问题是AD的自动布线完全无法胜任如此大体量的布线工作，最开始我们根据体量希望能够采用双面板来降低布线难度，然而实验室很难提供相关的加工工具。因此我们选择单面板布线，并只能采用手动布线方式，整个布线过程浪费了整整一周的时间。

布线中的另一个方面的困难是线宽的选择，一方面TPS54160不到15mil的引脚宽度要求布线最小宽度小于
15mil，另一方面BTN大电流供电要求布线宽度尽可能宽，经过一系列的调整和选择，我们确定了适合负载电流的
布线宽度，保证每一条支路的电流不过载。然而，10mil的线宽虽然满足了大部分的需求，却对后续打孔，焊接
的技术难度带来了巨大的麻烦。另外，开始布线时部分地方布线过密，导致出现了VCC，GND之间距离过小的问
题，之后的PCB对这些部分尽可能的进行了调整。

之后是PCB的印制工作，在小学期开始前，我们曾请教过助教有关大体量密集PCB雕刻的问题，发现抵达了雕刻机
的上限，之后学期内具体采用的是转印-腐蚀方式，然而这种方式对于技术水平仍有一定的要求，一方面，版面
过大导致散热过快，转印不能顺利实现，因此采取的解决方式是采用多次转印的方式确保转印实现。另一方面，
我们发现转印过程中由于线宽问题也可能导致一些线出现中断等问题，具体的解决方式是采用mark笔进行添加
等，并对PCB的连接情况进行了细致的检查。

之后的钻孔和焊接方面也遇到了相当大的困难，一方面超过200个孔使得钻孔体力消耗相当大，另一方面孔径过
小，焊盘过小导致钻孔伤及焊盘。这些问题我们通过自身的努力都已经尽可能的解决和避免了。焊接过程中，首
先遇到的问题是SMT的焊接工作。以TPS54160为例，其宽度为3mm，一侧共有5个引脚，引脚宽度和引脚之间的间
隙均不超过20mil，不仅如此，其下部还有一个散热引脚。初次焊接出现了巨大的问题，在助教的帮助下完成了
第一个芯片的焊接，然而后续的焊接也非常的吃力。这个问题的解决方式是我们取李兆基大楼找电子工艺实习的
师傅学习了一天的SMT焊接技术，并顺利完成了相关的焊接操作，使得该项技术达到了实用层次，如图\ref{ex}是我们的最终成果。

\begin{wrapfigure}{r}{0pt}
    \centering
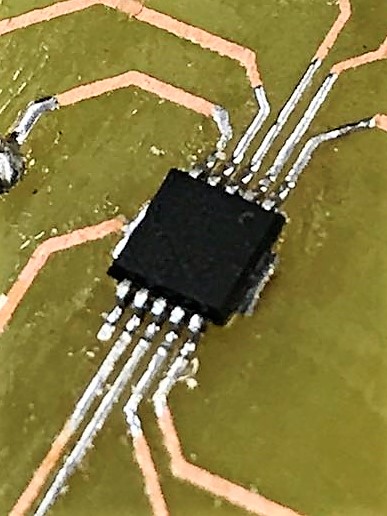
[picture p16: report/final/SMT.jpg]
    
    \caption{手焊SMT\ \ 11脚芯片TPS54160图}
    \label{ex}
\end{wrapfigure}
焊接技术的另一个问题是插接件焊盘丢失的问题，一些插接件由于打孔的问题出现了焊盘的不完整等问题。具体
的解决方式很大程度上依靠了陈崴同学优秀的焊接技术，同时，对于完成焊接的电路，进行逐点测试短路并对短
路部分予以隔断。同时对可能存在的电流容量不足的线路进行了上锡保证导电性。

电路组装完成后，仍然出现了大量的问题，首先解决了大量的虚焊，短路的问题。其次，为了固定摄像头模块，
我们在PCB上预留了相关位置，然而由于原理图出现镜像对称问题，摄像头前后两排引脚翻转，导致摄像头被反
向上电出现了一些损坏。为了解决这个问题，我们不得不设计另一个PCB将摄像头引脚反置，然而， 由于开始设
计的过程中没有考虑这方面的问题，导致新构建的PCB遮挡了一些排针和引脚，这个问题的解决方法是我们另购
了L形排针，将本来直插的排针改良为横接，基本上解决了这个问题。

在电路实际运行的过程中，我们发现由于电机驱动力不足，我们不得不提高PWM占空比来提升电机电流，然而，
当电流过大时电源电压被拉低导致后续电路失效供电失败，这个问题的解决方法是严格控制电机PWM占空比， 保
证了电路可以正常运行。另外，我们进一步处理了电路接触不良的问题，由于具体的问题和解决方法比较简单，
这里省略。
\section{项目创新点}
\subsection{摄像头的编写}
目前市场上存在的图像传感器的封装各式各样，在选购外设时，我们综合考虑了性能、成本、引脚数量、开发
难度等因素，最终选择了18脚封装的带有FIFO芯片的ov7670摄像头。这款外设由于封装较浅，所以价格也比较
低（约70元），在满足性能要求的前提下引脚数目也相对较少。虽然该摄像头在硬件层面很接近底层，开发难度
比其他深封装、外部接口简单、甚至自身带有MCU的传感器要高出许多，但预计不会超出能力所及。
在开发时也对比了FPGA和单片机，虽然单片机使用高级语言编写代码，逻辑控制会简单不少，但普通单片机的
晶振频率要比FPGA低，IO速度也比较慢，如果还需要与FPGA进行通信则更加麻烦。因此最终选择使用FPGA来
进行开发，既能与其他模块更好地整合，又避免了与单片机通信造成的资源浪费。
\subsection{上位机的编写}
\begin{wrapfigure}{r}{0pt}
    \centering
    
    \caption{上位机的用户界面}
    \label{UI}
\end{wrapfigure}
我们采用C++/Qt编写了自己的上位机程序负责遥控，图像解算，图像显示和图像存储。相比其他小组采用的手机端下载的成型APP，我们自行开发的程序可定制性更强，效率更高。同时，不论采用串口和蓝牙，回传的数据量解算都是相当大的，采用现成的程序根本无法完成相关任务。我们通过不断的调试，采用了多线程技术来采集，解算，显示图像，保证了上位机工作的稳定性和效率，保证上位机不成为整个项目的瓶颈。

同时我们编写了精美的用户界面，方便用户通过键盘和鼠标进行控制小车的速度。整个上位机的工作量甚至在一定程度上超过了C++小学期同类型大作业的工作量，并涉及到大量的API，如蓝牙，串口，以及openGL等软件工程技术，提高了我们的软件能力以及软件和硬件交互能力。上位机的用户界面如图\ref{UI}所示。
\subsection{PCB的处理}
我们设计了一块整合的PCB，包括三个开关电源，一个驱动电路和若干外围电路。采用TPS54160电源模块，虽然极大的增大了开发的难度，但是提高了电源的效率，比起线性电源不到50\%，甚至更低，仅为30\%的效率，我们的理论效率可以达到84\%。同时，通过将PCB的整合，我们尽可能的避免了飞线等情况，提升了电路的稳定性。整个PCB的难度和体量均为整个课程组里最大的之一。
\section{工作日志}
简要的工作日志如表\ref{commit}所示，由于我们采用了免费、开源的分布式版本控制系统Git，并将\href
{https://github.com/ZeroWeight/Project-of-Electronic-Circuits}{\underline{所有代码}}托管在
面
向开源及私有软件项目的托管平台Github中，我们可以很简单的管理我们的工程以及检查我们的进度，同时有效
加速团队间的协作进度以及防止可能存在的错误修改，提高开发效率。详细的工作日志如\href{log.pdf}
{\underline{附加文件}}所示。详细的工作日志请参阅\href
{https://github.com/ZeroWeight/Project-of-Electronic-Circuits/commits/master}{\underline
{提交记录}}
\begin{table}
    \centering
    \caption{工作日志表}\label{commit}
    \begin{tabular}{|m{1em}<{\centering}|m{1em}<{\centering}|m{4em}<{\centering}|m{4em}<{\centering}|m{4em}<{\centering}|m{4em}<{\centering}|m{4em}<{\centering}|}
        \hline
        \multicolumn{2}{|m{2em}<{\centering}}{小学期之前}&\multicolumn{5}{|m{25em}<{\centering}|}{
            主要完成了蓝牙模块，摄像头模块，上位机，电路原理图
            和PCB布线的分模块的工作，并分模块进行了检验，其中上
            位机顺带完成了一个上位机自检测试程序。基于WEBENCH完
            成了电源模块的设计，并综合了电机驱动到一块PCB上，完成
            了复杂的布线工作，为小学期做好了相关的准备
            }\\
        \hline
        \multicolumn{2}{|c|}{\diagbox{周}{工作}{日}}&周一&周二&周三&周四&周五\\
        \hline
        \multirow{2}{1em}{第一周}&上午
        &
            综合了假期的工作进度，摄像头模块和上位机模块进行了联调
        &
            PCB版印刷完毕，检查相关问题以及准备打孔工作
        &
            审查PCB发现PCB出现印刷质量问题，发回实验室重新制作
        &
            赴李兆基大楼完成SMT以及绝大部分插接件的焊接工作
        &
            修正PCB问题和错误，整车组装空载测试
        \\ 
        \cline{2-7}
        & 下午
        &
            PCB原理图交付实验室印刷，上位机模块发布稳定版本提供后续使用
        &
            PCB打孔，焊接工作（包括SMT焊接以及插接件焊接）
        &
            赴李兆基大楼进行PCB打孔，刷松香以及学习SMT相关焊接技术并进行练习
        &
            完成PCB的焊接工作，检查PCB电路的工作性能并进行调整
        &
            赴中发电子市场购买其他电子元件，并为实验室提供相关电子元件
        \\ 
        \hline
        \multirow{2}{1em}{第二周}&上午
        &
            完成基于LabVIEW (myRIO) 的陀螺仪配置
        &
            小车落地遥控，检查通信协议，准备验收
        &
            验收
        &
            视频录制，器件归还
        &
            展示工作
        \\ 
        \cline{2-7}
        &下午
        &
            设计完成红外测速功能
        &
            修正电路，检查蓝牙速度上线，寻找代替蓝牙信道的替代方式，通报验收
        &
            休整，准备项目结题
        &
            制作展示PPT，器件归还
        &
            -- --
        \\ 
        \hline
    \end{tabular}
\end{table}
\section{项目总结和感想}
经过两周的努力以及之前的一些铺垫，我们完成了整个项目从规划设计到具体实现的各种环节，有了比较大的收
获。

首先是项目的规划，跟进方面。在项目规划过程中，我们在7月份就提出了一份明确的规划方案，之后的工作均
按照方案实行。在合作方面，我们队友之间配合紧密，合理的采用了Github等团队合作，代码托管工具加速了我
们的合作进程。技术水平的相近保证了我们团队分工均匀有效，每个人都可以发挥自己的特长。模块分工清晰明
确，陈崴同学负责了几乎所有的Verilog代码的实现，而张蔚桐负责了所有的上位机实现和模拟电路部分。这种
分工方式使得我们不论是合并工作量还是检查错误都有着明确的方向，也不会发生队友之间相互“甩锅”的情况。

其次是对于硬件软件电路的关系的理解，通过这个项目我们了解到，虽然相比于模拟电路，数字电路的稳定性和
可展示性更强；相比于硬件底层的封装，同样工作量的软件工程，或者是顶层的综合更加“出彩”，但是模拟电
路，底层封装的重要性是不可忽视的。底层电路是整个项目的基础，更好的了解底层的情况有助于我们对顶层进
行更好的封装。例如，我们采用的摄像头模块是18引脚的底层封装，相比于其他组用的高级摄像头模块，带来了
大量的工作量，然而，我们的摄像头造价更低，不考虑其他硬件瓶颈限制，我们的摄像头采集速度也更快，采集方式也更灵活。

这次课程设计，我们从底层硬件电路层面到上位机纯软件层面进行了设计，实现了一个从硬件到软件有机整合的
项目，也得到了相比于之前做的软件项目不同的进步。通过和硬件层面的了解，我们了解到一些事实存在的行业瓶颈，了解到了软硬件结合的过程中硬件电路的重要性。通过实际硬件电路的了解，设计，制作这些过程，我们增长了硬件电路调试设计的很多经验，如PCB设计的合理性等，方便了我们之后进一步的硬件项目的设计。

最后的最后，我们发现尤其是对硬件部分，性能上的需求是远远高于实际的实现的，本次设计过程的过程中我们克服了大量的硬件瓶颈问题，例如蓝牙模块，上位机速度问题。生产更高速，更小型化，更稳定的硬件模块，例如研发更高速的无线通信方式，如目前正在逐步推进的5G网络等，永远是硬件领域的核心的，最意义的发展方向，也希望我们之后能够在此领域内做出自己的微小的贡献！
\section{项目完成情况}
项目完成情况良好，小车模型如下图所示。蓝牙图像回传收到前面提到的数据量和速度的问题受限，采用串口代
替蓝牙可以得到比较好的图像，一些图像如下页所示，作品视频可以参考\href{final.mp4}{\underline{视频
文件}}
\begin{figure}[h]
    \centering
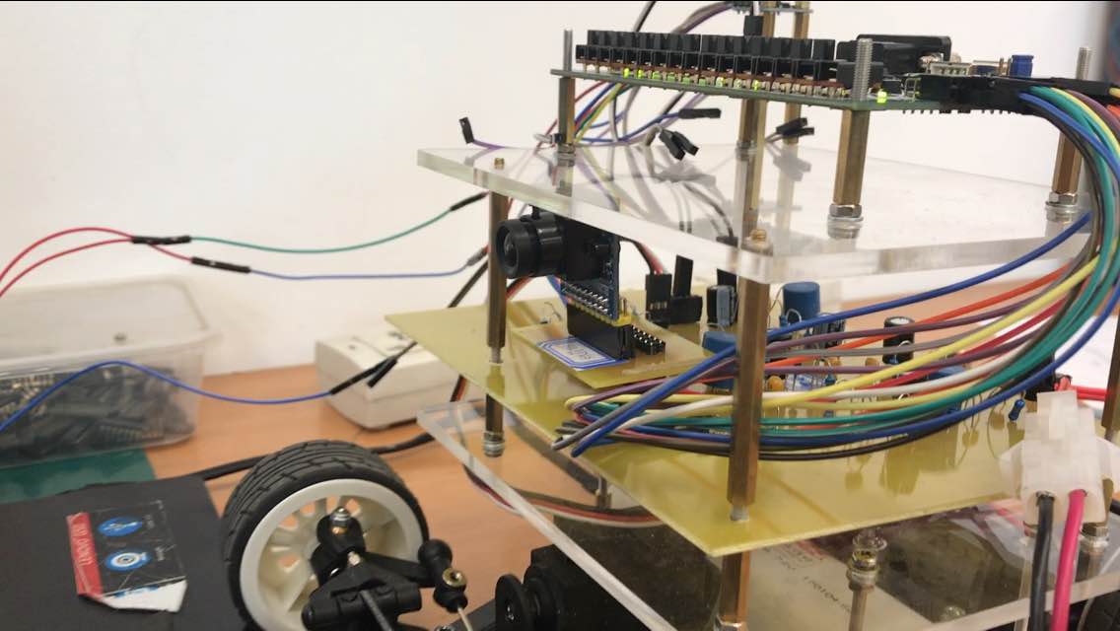
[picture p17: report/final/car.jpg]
    
    \caption{小车最终模型}
\end{figure}
\clearpage
\vspace{5ex}
\begin{multicols}{2}
    \begin{figure}[H]
        \centering
        
    \end{figure}
    \begin{figure}[H]
        \centering
        
    \end{figure}
\end{multicols}
\vspace{5ex}
\begin{multicols}{2}
    \begin{figure}[H]
        \centering
        
    \end{figure}
    \begin{figure}[H]
        \centering
        
    \end{figure}
\end{multicols}
\end{document}

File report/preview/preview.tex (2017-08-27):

% compile with xelatex
\documentclass[a4paper]{paper}
\usepackage{ctex}
\usepackage{amsmath}
\usepackage{graphicx}
\usepackage{wrapfig}
\usepackage{multicol}
\usepackage{float}
\title{
    \begin{large}电子技术课程设计\end{large}\\
    基于受控无人车的场地探测和3D重建系统\\
    预习报告
}
\author{
    张蔚桐\ 2015011493\ 自55\\
    陈　崴\ 2015011481\ 自55
}
\begin {document}
\newcommand{\tabincell}[2]{\begin{tabular}{@{}#1@{}}#2\end{tabular}}
\maketitle
\tableofcontents    
\clearpage
\section{选题背景及课题简介}
根据《智能交通》和《智能家居》的课题方向，我们将选题定位为基于受控无人车的场地探测和3D重建系统。

\begin{wrapfigure}{r}{0pt}
    \centering
    
    \caption{“蝎形”（"scorpion"）机器人行进在福岛核电站2号反应堆内}
    \label{Robo}
\end{wrapfigure}
目前，受控无人车，即对无人车发送指令控制无人车的技术已经有了很多现实生活中的应用。然而，
这种受控无人车要求控制者能够看到无人车的运动状态，并对无人车进行控制。这样不方便无人车进一步
进行无人作业。例如，在地震灾区倒塌的房间中，控制人员无法看到无人车的具体位置，这就需要无人车
对周边环境数据进行采集，方便控制人员进行进一步的控制。另外，通过加装场地检测装置，无人车或
机器人可以到很多危险场合进行作业和信息的采集。例如，2011年日本福岛核泄漏之后，东电公司曾派遣如图
\ref{Robo}所示的机器人到反应堆内调查事故情况。通过加装摄像头和辐射监测设备，机器人可以在人类
无法承受的辐射量内进行高强度监测作业。

另外，目前3D检测和建模技术方兴未艾。利用无人机等设备对建筑物外表面进行3D检测建模的技术已经实现。
计算机视觉领域内，SfM(Shape from Motion)等基于单目摄像机的3D重建技术已经相对比较成熟，因此，
周边技术的成熟为我们的设计提供了相当的基础。同时，我们也考虑采集小车的位置信息，一方面，
对于控制人员来说，了解小车的行进路线（相对位置）也是一个很重要的信息点，另外一方面，根据计算机
的相关知识，我们也可以知道获取准确的拍摄角度和拍摄位置可以更好的加大3D重建的精度，而这方面的应用和算法
据我们所查阅的资料来看相对较少，可以进行进一步的创新。

因此我们将选题定位基于受控无人车的场地探测和3D重建系统，目标是通过控制无人车的行为，完成对场地内
图像信息的采集，并在合适的情况下允许上位机进行3D重建，完成对场景3D状态的描述工作。根据时间限制
和具体的完成情况，我们将整个项目分为如下几个部分进行。
\begin{enumerate}
    \item 第一部分
    \begin{itemize}
        \item 基本的电源管理和小车运动控制
        \item 在上位机控制下小车完成相关运动
        \item 小车安装摄像头，将图像回传上位机
    \end{itemize}
    \item 第二部分
    \begin{itemize}
        \item 图像实时回传
        \item 小车完成相对位置信息的记录和回传
        \item 利用位置信息进行二维地图的展示工作
    \end{itemize}
    \item 第三部分
    \begin{itemize}
        \item 将上位机应用部署到移动平台
        \item 小车安装避障系统，并可以自动运行
        \item 三维重建，同时利用位置信息
    \end{itemize}
\end{enumerate}
从上面我们可以看出整个工程量较大，受到两周的开发时间的限制可能不一定全部完成，剩余工程可以
作为参加挑战杯等进一步开发项目的发展方向。

\section{方案比较与选择}
\subsection{主控元件的选择}
首先我们考虑主控元件的选择，根据我们的技术水平和课题的情况，可供选择的主控芯片为MCU
（单片机）和FPGA。相比FPGA，MCU具有开发相对简单的优势，以串口通信协议为例，大部分MCU
的系统库中均已经封装了串口通信协议，而FPGA相对更接近底层，因此需要自行完成相关的通信协议
的封装，这将消耗大量的时间和精力。

然而，相比于MCU，FPGA在速度和并行性方面有着很大的优势。根据我们查阅的资料，以STMF103为例，
其时钟速度可以达到72MHz，然而由于串行执行的原因，IO速度相对于FPGA较低；对比我们使用的Xilinx
FPGA，其时钟速度可以达到100MHz，同时高度并行使得模块之间互相不干扰，保证了IO速度等要求。

因此，考虑到性能要求以及课程需要，我们在硬件方面采用了FPGA作为主控进行开发。
\subsection{通信机制的选择}
根据查阅的资料，可供选择的无线通信机制有如下三种：

\begin{enumerate}
    \item WiFi信道

    这种通信机制需要将WiFi模块植入硬件，使得小车可以联网传输信息。
    上位机或移动平台使用WiFi下载信息。这种方式的优势一方面是信息传输距离较远，
    在一个路由器覆盖的范围内，信息均可以被传输。另一方面可拓展性也比较强，
    如果设计了合理的联网方式，将进一步解除距离限制，通过将信息上传到云空间，
    用户可以在任何联网的地区完成信息的收取和对小车的控制。

    这种通信机制的缺点是过于复杂，尤其是使用FPGA进行开发的情况下，网络通信协议
    将带来更大的开发时间消耗，不适用于本课程的短期开发。

    \item 蓝牙信道

    这种通信机制利用蓝牙模块，蓝牙模块已经将蓝牙信道封装成串口的形式，
    从很大程度上方便了开发。同时，通过对电脑，移动设备上的蓝牙模块进行开发，
    用户可以不依赖于第三方设备（如路由器）和小车进行通信。虽然通信速度上相比WiFi也
    有一定的损失，并且通信距离受到明显限制，但相比于WiFi模块而言，其功耗更小。

    \item SPI信道

    后期的开发表明，蓝牙的速度并不能保证摄像头传输的实时性，因此后期考虑采用SPI信道
    替代原有的蓝牙信道，然而相比于蓝牙——串口信道，SPI的开发不论是在上位机方面还是在
    FPGA方面均比较复杂，因此不一定可以完成。

\end{enumerate}
综合以上三种通信机制的优缺点，我们选择蓝牙信道作为通信手段。
\subsection{供电方式的选择}
首先通过查阅可能使用到的外设的技术手册，我们大概确定了供电需求为
\begin{itemize}
    \item 5V@1.5A
    \item 3.3V@1.5A
    \item 7.2V@40A
\end{itemize}
其中5V@1.5A负责向FPGA 5V@1A以及舵机供电，3.3V电源负责向外设供电，例如我们采用的摄像头OV7670
采用的供电电压为3.3V@100mA。7.2V@40A电源负责向电机供电，并应接受PWM调制来控制电机转速。

通过查阅资料我们发现，供电的难点在7.2V@40A电源，而5V@1.5A电源和3.3V@1.5A电源
均可以使用实验室提供的TPS54160 SMT芯片完成设计，
这一部分内容将在后面基于Webench的仿真实现上面进行说明。7.2V@40A电源的电流限额主要受到电机供电电流要求
影响，从实验室提供的数据手册我们可以发现，电机的空载电流2.4A，最高效率电流11A，堵转电流52.8A，根据网上
查阅的相关资料，电机的限流应当是最高效率电流的约4倍，因此设计7.2V@40A电源负责向电机供电。

这里讨论7.2V@40A电源的设计问题。因为需要接受PWM信号调制，因此我们采用了H桥进行设计。
\begin{wrapfigure}{r}{0pt}
    \centering
    
    \caption{H桥的电路原理图}
    \label{H-bridge}
\end{wrapfigure}
H桥的电路原理图如图\ref{H-bridge}所示。Q1\~Q4可以由处于饱和状态的三极管或开关状态的MOS管组成 
J1 和 J2 分别接入前一级驱动电路产生的两个反相PWM，设某时刻 J1 为高电平，
则 Q3 导通，Q1 截止；由于反相，J2 为低电平，Q2 导通，Q4 截止，
电流由通过 Q2，经负载，再经过 Q3 流入地。
同理，当某时刻 J1 为低电平时，Q1,Q4 导通， Q2,Q3 截止，
电流依次经 Q1,R1,Q4 流入地。综上，任意时刻有且只有一个对角线上的两个MOS管是导通的。

对于电机，我们可以设定刹车模式，即可以通过与上述方法类似的方法将电机两脚短路，使得电机
迅速产生电磁制动实现刹车效果

通过搜索符合要求的元件，我们发现合理的解决方案为bts7960/7961芯片和自行搭建H桥两种方案。

bts7960/7961芯片是接受5VPWM信号调制的，输入电压5.5V至27V@43A的半H桥电路，
采用SMT封装，输出电流符合要求。
然而，由于我们电机的额定输入电压为7.2V，经过对电机的初步调试我们可以发现
电机在7.2V输入电压下的转速非常高，导致速度不能得到控制，
经过进一步的实验我们发现，在低于数据手册上提供的5.4V供电的情况下，
电机的转速可以保证一个理想的状态，因此可以初步得到结论即PWM信号的占空比不可过高。

而自行搭建H桥，因为工艺比较复杂，同时在网上找不到合适的大功率MOS管供应商，
因此我们放弃了这个方案。

\subsection{摄像头数据传输技术的选择}
我们采用的OV7670摄像头，可以输出25fps 640*480 VGA格式的RGB三色图像，输出采用8线同步并行传送
因此输出时钟速度可以达到$25*640*480 \approx 8\mathrm{MHz}$。
收到蓝牙信道是串行接口的原因，蓝牙信道的速度必须达到8MB/s，这是一般蓝牙系统很难做到的。
因此不论是FPGA读取信息还是蓝牙传输信息的速度，均不如摄像头采集数据的速度，需要找到合理的解决方式。

经过我们查阅相关资料发现，OV7670的传输方式有如下三种形式：
\begin{wrapfigure}{r}{0pt}
        \centering
        
        \caption{MCU/FPGA直接采集}
        \label{fig2}
        
        \caption{FIFO采集}
        \label{fig3}
\end{wrapfigure}
\begin{itemize}
    \item MCU/FPGA直接采集：

    如图\ref{fig2}所示，这种方法是最简单，最直接，但也是最不好实现的方法，
    以MCU为例，多数的CMOS 芯片（如OV7670）的时钟速度可高达24M，
    一般MCU的IO 端口速度根本不可能达到，所以需要高速MCU。
    这对多数用户来讲有些不现实。但也不是完全没有办法在低速上实现采集，
    方法也很简单，那么就是降低CMOS的输出速度，
    不过这需要靠外部的晶振和内部的PLL电路以及像素时钟速度，
    帧速等多个寄存器共同设置，并且要和MCU的IO速度匹配才可实现。
    但这么做将带来巨大的寄存器设置工作量并导致硬件图像的采集速度
    可能下降到0.5帧以下，同时带来图像失真的可能。
\end{itemize} 

\begin{itemize}
    \item DMA方式

    这种方式主要用于MCU中，FPGA中这种方式效果不明显，DMA控制器使得数据
    可以绕过CPU直接进入内存，但是在FPGA中，同时受到串口通信速度的影响，
    这种方式效果也不是很明显。

    \item FIFO模块采集

    如图\ref{fig3}，用户只需要按上述时序图控制相关的几个控制引脚即可，可以很
    方便的使用在低速MCU上，另外一个好处是，可以直接IO口读取数据，
    读出的数据可以直接送屏，也可以经过MCU简单处理；当然也可以不经过
    MCU，直接送到屏等外围器件使用。对于FPGA，以及速度相对较低的串口单元，
    使用FIFO也能很大程度的解决速度不同步的问题。

\end{itemize}
\subsection{车辆位置角度信息处理方式的选择}
为了进一步增强3D建模的精度，我们希望能够采集车辆的位置信息和角度信息。
由于摄像头和车辆是相对固定的，这样也就获得了摄像头的位置信息和角度信息。

根据我们查阅到的资料，车辆的位置信息和角度信息有几种不同的获取方式，如下所示。
\begin{itemize}
    \item 惯性测量单元（IMU）模块

    通过加速度计和陀螺仪的信息，可以直接读取车辆的加速度和角度。
    经过积分之后可以得到车辆的速度信息和角度信息，这种方法最简单，
    但是误差最大，加速度计易受到颠簸，碰撞，刹车等造成的脉冲影响，
    并进一步影响积分的准确性。角速度计（陀螺仪）具有一般性的零点迁移
    问题，这包括动态的零点波动和静态的温漂。经过积分会导致角度信息
    相当不准确。这种方法只能作为一种简单的参考，实用时必须加以处理。

    \item 磁场计

    通过对地磁角度的测定，可以直接获取车辆的角度，并通过加速度计等
    方式获得车辆的速度，这种方式误差相对前一种较小，
    但是受外界磁场的影响比较严重，尤其是当存在10A绕组的电机驱动时，
    这种方法可以认为无效。

    \item 码盘

    这种方法通过测量车辆四轮的转速经过解算得到车辆的具体位置，相比于
    之前几种方式，这种方式依赖于更加准确的光电传感器，因此得到的值也
    相对比较准确，这种方法的难点在于必须对车辆的刚性模型进行建模，
    同时安装码盘也是一个硬件上的难点。
\end{itemize}
综合提到的几种方法，我们计划采取IMU+信号处理+码盘解算几种方式
得到车辆的具体位置，希望通过反馈等方式希望得到更准确的车辆控制。

\subsection{其他注意事项}
在设计对车辆相对位置进行测量的过程中，考虑到FPGA在解算浮点数方面比较难以开发，
我们选用了NI myRIO进行解算和控制，并采用myRIO自带的WiFi进行相关数据的回传。

NI myRIO是NI针对教学和学生创新应用而最新推出的嵌入式系统开发平台。
NI myRIO内嵌Xilinx Zynq芯片，使学生可以利用双核ARM Cortex-A9的
实时性能以及Xilinx FPGA可定制化I/O，学习从简单嵌入式系统开发到
具有一定复杂度的系统设计，采用LabView语言进行可视化编程。
通过myRIO可以大幅简化控制算法如PID的调试过程，显著降低开发难度，加速开发进度。

\section{基于FPGA的数字系统框图}
\begin{figure}
    \centering
    
    \caption{基于FPGA的数字系统框图}
    \label{FPGABlockDesign}
\end{figure}
如图\ref{FPGABlockDesign}所示，左侧为封装的顶层模块，从右侧可以看出共分为8个子模块。
\begin{itemize}
    \item CLK\_GEN

    该模块对100MHz系统时钟分频，输出4个时钟分别供串口、舵机、电机、摄像头使用。

    \item UART\_RX

    蓝牙串口接收模块，RX为数据线，每从上位机接收一个码元即触发finish信号，并将数据存
    在data寄存器供其他模块使用。同时内部还提供了一个error接口，接收数据发生错误时触发。

    \item UART\_TX

    蓝牙串口发送模块，TX为数据线，当触发start信号后，将data寄存器中的内容发送给上位机，
    发送完成后会得到一个finish信号反馈。

    \item SERVO

    舵机控制模块，从串口接收转向控制指令，输出舵机PWM信号。

    \item MOTOR

    电机控制模块，同样从串口接收指令，输出电机使能和PWM信号。

    \item OV\_INIT

    摄像头初始化模块，SCL和SDA为SCCB协议的时钟线和数据线，初始化前initialized\_flag为
    低电平，OV\_STORE和OV\_READ处于失能状态，初始化完成后拉高initialized\_flag，摄像头
    便可正常工作。

    \item OV\_STORE

    将摄像头采集到的图像存储于FIFO中，存储完成一帧后触发new\_frame\_flag信号，等待FPGA
    读取图像结束后才继续采集下一帧。

    \item OV\_READ

    从FIFO中读取一帧图像，并存储在frame\_data寄存器中，读取完成后触发两个信号，一个是
    frame\_read\_flag，通知摄像头可以继续采集下一帧图像，另一个是new\_frame\_data\_flag，
    通知顶层模块将读取到的数据发送给上位机。
    
\end{itemize}
\section{传感器/执行机构接口电路图}
\subsection{传感器电路}
\subsubsection{数字接口电路}
\begin{wrapfigure}{r}{0pt}
    \centering
    
    \caption{OV上拉电阻和转接电路}
    \label{OV}
\end{wrapfigure}
这部分主要是完成数字模块之间的接口电路，由于各个数字模块已经将输出电平统一标准化为TTL电平，
因此这部分的关键主要是接口通信协议的实现，主要有FPGA方面实现了SCCB接口通信协议，串口通信协议，
摄像头数据读取协议等。另外，SIO\_C和SIO\_D分别为SCCB总线的时钟线和数据线，为了
方面对多个设备进行控制，OV的SCCB两个端口采用的均是OC门输出，需要上拉4.7k
电阻实现输出高低电平，这些需要在设计PCB的时候尽可能的考虑到并保证接线的
稳定性和摄像头位置的稳定性，因此需要在PCB上统一制作并提供对FPGA的简单的接线电路，这部分的电路
可以如图\ref{OV}所示。

\begin{wrapfigure}{r}{0pt}
    \centering
    
    \caption{74HC244驱动器电路}
    \label{motor0}
\end{wrapfigure}
另一部分的接口电路问题是3.3V电平标准和5V电平不匹配的问题以及同时设计到的FPGA驱动能力不足的问题
通过查阅给定的技术手册我们发现FPGA输入电流1A，标准的输出电压为3.3V，
而不论是电机驱动的PWM还是舵机驱动的PWM均为5V，这中间需要设计适当的接口
电路，同时，由于工程量比较大，担心FPGA会出现总线电流过大或无法驱动相关
接口电路的情况，因此我们采用了74HC244芯片作为接口的辅助电路，74HC244是
一款高速CMOS驱动芯片，支持三态门使能，通过HC244我们可以顺利的将3.3V输出转化为5V，
并提升驱动能力。根据74HC244的接线要求，我们在输入端接入下拉电阻1k实现相关功能。这部分的电路
有如图\ref{motor0}所示。同时我们将剩下的74HC244引脚同样通过排针引出，留待之后使用。

\subsubsection{模拟接口电路}
\begin{wrapfigure}{r}{0pt}
    \centering
    
    \caption{ENC-03模块外部电路图}
    \label{ENC}
\end{wrapfigure}
我们计划采用输出模拟电压的ENC-03陀螺仪，这是是一种应用科氏力原理的角速度传感器，
陀螺输出一个和角速度成正比的模拟电压信号。通过积分电路可以得到相关的角度等。根据ENC-03
技术手册，我们设计输出放大电路如图\ref{ENC}所示，整个电路由两个滤波器组成，左侧为低通滤波器，
用于滤除传感器高频噪声，右侧为高通滤波-放大电路，用于放大电压信号和滤除低频温漂。

进一步，我们搭建基本积分电路可以得到角度信息，两个信息通过AD模块可以返回给主控设备。
由于我们计划采用myRIO进行位置信息的测量，因此这部分可以直接使用LabVIEW语言在myRIO上完成，
就没有设计电路的必要了。

\subsection{执行接口电路}
这部分主要描述的是对电机和舵机的驱动电路

对于舵机驱动，单片机输出高电平为3.3V的PWM脉冲，经过前文提到过的74HC模块转5V驱动舵机旋转。

\begin{wrapfigure}{r}{0pt}
    \centering
    
    \caption{电机驱动电路}
    \label{motor1}
\end{wrapfigure}
对于电机驱动，我们使用BTN7970模块，如图\ref{motor1}所示。这里为了方便后文叙述，两片IN引脚被
命名为IN1，IN2，两片INT引脚被命名为INT1,INT2。我们将INT1,INT2短接并输入PWM波形控制电机转动速度。
将IN1，IN2分别接高低电平控制电机正转反转。例如\{INT1 = 0,INT2 = 1\}代表电机正转，\{INT1 = 1,
INT2 = 0\}代表电机反转。当\{INT1 = 0,INT2 = 0\}时，H桥全部关断，表示不控制电机转动。
当\{INT1 = 1,INT2 = 1\}时，H桥下部导通，电机两端短接，使得电机的机械能通过电磁感应和短路线
迅速释放，实现刹车功能。BTN相关引脚仍为5V接线，因此使用74HC244完成相关的电平转换和放大工作。
\section{基于Webench的电源电路仿真}
WEBENCH是TI公司提供的设计环境，通过软件工具提供定制电源等的设计，通过使用WEBENCH可以
提升设计效率。整体的设计思路如下：
\begin{itemize}
    \item 输入电压的确定

    我们将电池断开，测量电压约为8.2V，将电池直接接电机，并在电机上施加比较大的阻力，发现
    电源电压约为7V，因此我们设计电源时考虑输入电压为6V\~9V即可满足需求。

    \item 输出电压的确定

    由表\ref{t1}所示，我们需要向FPGA提供5V外接电源，对舵机提供5V外接电源，
    对外设提供3.3V外接电源，因此设计输出电压为5V，3.3V。

    \item 输出电流的确定

    首先根据实验室提供的TI样片，我们选择了TI TPS54160降压模块，TPS54160器件是一款带有集成型
    高侧MOSFET的60V,1.5A的降压稳压器。电流模式控制提供了简单外部补偿和灵活组件选择，功耗较小。

    根据TPS54160的输出电流，我们限制电源输出电流为1.5A。同时查阅技术手册可以得到主要的部件
    的供电信息如表\ref{t1}所示,总计需要输出电流5V@2A,3.3V@500mA，因此需要设计两路5V供电电源，
    其中一路FPGA自用（包括驱动器74HC244），一路给舵机/外设使用。

\end{itemize}
因此，进入WEBENCH中提供需求的输入，输出信息，选择器件为TPS54160，可以得到元件的原理图。
通过调整原理图上的元件的值的信息，可以选用已有阻值的元件进行仿真，最终确定的电路原理图和
响应时间仿真和稳态仿真如下面几张图所示。两个电路结构相同，相关参数差别如表\ref{t2}所示。
整理仿真结果如表\ref{t3}所示。可以看出电源的性能效果还是比较理想的，可以进行实际电路的搭建。
\begin{figure}
    \centering
    
\end{figure}
\begin{multicols}{2}
    \begin{table}[H]
        \centering
        \caption{主要部件供电信息}
        \label{t1}
        \begin{tabular}{|c|c|c|} \hline
            部件& 电压& 电流\\ \hline
            FPGA& 5V& 1A \\ \hline
            舵机& 5V & 800mA \\ \hline
            74HC244 & 5V& 100mA\\ \hline
            蓝牙模块 & 5V& 100mA\\ \hline
            OV7670& 3.3V& 200mA \\ \hline
        \end{tabular}
    \end{table}
    \begin{table}[H]
        \centering
        \caption{仿真主要性能指标}
        \label{t3}
        \begin{tabular}{|c|c|c|} \hline
            参数&3.3V电源&5V电源\\ \hline
            稳态电压平均值& 3.435V&5.326V\\ \hline
            稳态电压峰峰值& 3.648mV &2.465mV\\ \hline
            启动时间& 1.368ms&2.379ms\\ \hline
            电感电流峰值& 1.245A&1.753A\\ \hline
        \end{tabular}
    \end{table}
\end{multicols}
\clearpage
\begin{table}
    \centering
    \caption{元件参数信息}
    \label{t2}
    \begin{tabular}{|c|c|c|c|} \hline
        元件名&类别/单位& 3.3V电源& 5V电源\\ \hline
        Cin&电解电容/$\mu$F&470&470\\ \hline
        Rent&定值电阻/k$\Omega$&110&110\\ \hline
        RenB&定值电阻/k$\Omega$&33&33\\ \hline
        Ccomp&独石电容/nF&1&1\\ \hline
        Ccomp2&独石电容/pF&10&10\\ \hline
        Rcomp&定值电阻/k$\Omega$&33&56\\ \hline
        Css&独石电容/nF&6.8&6.8\\ \hline
        Rt&定值电阻/k$\Omega$&110&110\\ \hline
        Cboot&独石电容/nF&100&100\\ \hline
        D1&肖特基二极管/型号&SS24FL&SS24FL\\ \hline
        L1&定值电感/$\mu$H&100&100\\ \hline
        Rfbt&定值电阻/k$\Omega$&33&56\\ \hline
        Rfbb&定值电阻/k$\Omega$&10&10\\ \hline
        Cout&电解电容/$\mu$F&470&470\\ \hline
    \end{tabular}
\end{table}
\begin{multicols}{2}
    \begin{figure}[H]
        \centering
        
        \caption{5V电源启动情况}
    \end{figure}
    \begin{figure}[H]
        \centering
        
        \caption{5V电源稳态情况}
    \end{figure}
    \begin{figure}[H]
        \centering
        
        \caption{3.3V电源启动情况}
    \end{figure}
    \begin{figure}[H]
        \centering
        
        \caption{3.3V电源稳态情况}
    \end{figure}
\end{multicols}
\section{PCB的设计制作}
完成了电源模块的仿真之后就可以开始着手进行PCB的设计制作了，在设计制作的过程中，由于考虑到
手工焊接的困难，因此尽可能多的选用了插接件代替SMT封装元件，如电阻，电容等，同时，根据走线可能
涉及的电流大小如图\ref{fig4}所示，我们设计走线宽度为
\begin{itemize}
    \item 对BTN驱动板，走线40mil(1mm)，对应电流3A左右
    \item 对电源管理模块，走线15mil(0.4mm)，引脚处走线10mil(0.25mm)，对应电流1.5A左右
\end{itemize}
同时对大电流部分加焊锡保护走线，防止过热。整版PCB单面布线，背面加装散热片，保证散热顺畅并注意
IC散热引脚接触良好。同时考虑接线端子，IC等的位置关系，充分考虑日后安装，打孔位置，
保证接线顺利同时散热合理。PCB如图\ref{pcb}所示。
\begin{table}
    \centering
    \caption{PCB线宽和电流的关系}
    \label{fig4}
    \begin{tabular}{|c|c|c|c|c|c|} \hline
        电流(A)&线宽(mm)&电流(A)&线宽(mm)\\ \hline
        6.0&2.5&5.1&2.0\\ \hline
        4.2&1.5&3.6&1.2\\ \hline
        3.3&1.0&2.8&0.8\\ \hline
        2.3&0.6&2&0.5\\ \hline
        1.7&0.4&1.3&0.3\\ \hline
        0.9&0.2&0.7&0.15\\ \hline
    \end{tabular}
\end{table}
\begin{figure}
    \centering
    
    \caption{PCB版效果图}
    \label{pcb}
\end{figure}
\end{document}

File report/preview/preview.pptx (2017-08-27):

## 基于受控无人车的 场地探测和三维重建系统

张蔚桐 2015011493 自55
陈　崴 2015011481 自55

## 一、选题背景

- 受控无人车已有许多现实应用
  - 要求控制者看到无人车运动状态
- 采集环境数据，方便人员控制
- 可到危险场合作业和采集信息
  - 日本蝎形机器人探查福岛废弃核反应堆
- 三维检测和建模技术方兴未艾
- 获取小车位置，提高建模精度

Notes: 根据《智能交通》和《智能家居》的课题方向，我们将选题定位为基于受控 无人车的场地探测和 3D 重建系统。
目前，受控无人车，即对无人车
发送指令控制无人车的技术已经有
了很多现实生活中的应用。然而，这
种受控无人车要求控制者能够看到
无人车的运动状态，并对无人车进
行控制。这样不方便无人车进一步
进行无人作业。例如，在地震灾区倒
塌的房间中，控制人员无法看到无人
车的具体位置，这就需要无人车对周
边环境数据进行采集，方便控制人员
进行进一步的控制。另外，通过加装
场地检测装置，无人车或机器人可
以到很多危险场合进行作业和信息
的采集。例如，2011 年日本福岛核
泄漏之后，东电公司曾派遣如图 1所 示的机器人到反应堆内调查事故情况。通过加装摄像头和辐射监测设备，机 器人可以在人类无法承受的辐射量内进行高强度监测作业。
另外，目前 3D 检测和建模技术方兴未艾。利用无人机等设备对建筑物 外表面进行 3D 检测建模的技术已经实现。计算机视觉领域内，SfM(Shape from Motion) 等基于单目摄像机的 3D 重建技术已经相对比较成熟，因此， 周边技术的成熟为我们的设计提供了相当的基础。同时，我们也考虑采集小 车的位置信息，一方面，对于控制人员来说，了解小车的行进路线(相对位 置)也是一个很重要的信息点，另外一方面，根据计算机的相关知识，我们 也可以知道获取准确的拍摄角度和拍摄位置可以更好的加大 3D 重建的精 度，而这方面的应用和算法据我们所查阅的资料来看相对较少，可以进行进 一步的创新。
因此我们将选题定位基于受控无人车的场地探测和 3D 重建系统，目标 是通过控制无人车的行为，完成对场地内图像信息的采集，并在合适的情况 下允许上位机进行 3D 重建，完成对场景 3D 状态的描述工作。根据时间限 制和具体的完成情况，我们将整个项目分为如下几个部分进行。

## 二、预期完成内容

- 第一部分
  - 电源管理，小车运动控制
  - 上位机控制小车完成相关运动
  - 小车安装摄像头，将图像回传上位机

## 二、预期完成内容

- 第二部分
  - 图像实时回传
  - 小车完成相对位置信息的记录和回传
  - 利用位置信息进行二维地图的展示工作

## 二、预期完成内容

- 第三部分
  - 将上位机应用部署到移动平台
  - 小车安装避障系统，并可以自动运行
  - 利用位置信息进行三维重建

## 三、方案比较和选择

- 主控元件
- 通信机制
- 供电方式
- 摄像头数据传输技术
- 车辆位置信息处理方式
- 其他注意事项

## 主控元件

- MCU

- 系统库封装好，开发相对简单
- 时钟72MHz
- 串行执行，IO速度低

- FPGA

- 更接近底层，需自行封装模块
- 时钟100MHz
- 并行执行，IO速度高

√

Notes: 首先我们考虑主控元件的选择，根据我们的技术水平和课题的情况，可供选 择的主控芯片为 MCU (单片机)和 FPGA。相比 FPGA，MCU 具有开发 相对简单的优势，以串口通信协议为例，大部分 MCU 的系统库中均已经封 装了串口通信协议，而 FPGA 相对更接近底层，因此需要自行完成相关的 通信协议的封装，这将消耗大量的时间和精力。
然而，相比于 MCU，FPGA 在速度和并行性方面有着很大的优势。根 据我们查阅的资料，以 STMF103 为例，其时钟速度可以达到 72MHz，然而 由于串行执行的原因，IO 速度相对于 FPGA 较低;对比我们使用的 Xilinx FPGA，其时钟速度可以达到 100MHz，同时高度并行使得模块之间互相不 干扰，保证了 IO 速度等要求。
因此，考虑到性能要求以及课程需要，我们在硬件方面采用了 FPGA 作为主控进行开发。

## 三、方案比较和选择

- 主控元件
- 通信机制
- 供电方式
- 摄像头数据传输技术
- 车辆位置信息处理方式
- 其他注意事项

## 通信机制

- WiFi

- 通信速率高，传输距离远
- 可拓展性强
- 可封装成SPI协议，开发仍然较为困难

- 蓝牙

- 封装成串口协议，方便开发
- 不依赖第三方设备
- 功耗较小
- 通信速率较低，不能满足实时性
- 传输距离局限

√

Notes: WiFi 信道
这种通信机制需要将 WiFi 模块植入硬件，使得小车可以联网传输信 息。上位机或移动平台使用 WiFi 下载信息。这种方式的优势一方面 是信息传输距离较远，在一个路由器覆盖的范围内，信息均可以被传 输。另一方面可拓展性也比较强，如果设计了合理的联网方式，将进 一步解除距离限制，通过将信息上传到云空间，用户可以在任何联网 的地区完成信息的收取和对小车的控制。
这种通信机制的缺点是过于复杂，尤其是使用 FPGA 进行开发的情况 下，网络通信协议将带来更大的开发时间消耗，不适用于本课程的短 期开发。
蓝牙信道
这种通信机制利用蓝牙模块，蓝牙模块已经将蓝牙信道封装成串又的 形式，从很大程度上方便了开发。同时，通过对电脑，移动设备上的 蓝牙模块进行开发，用户可以不依赖于第三方设备(如路由器)和小 车进行通信。虽然通信速度上相比 WiFi 也有一定的损失，并且通信 距离受到明显限制，但相比于 WiFi 模块而言，其功耗更小。
SPI 信道
后期的开发表明，蓝牙的速度并不能保证摄像头传输的实时性，因此 后期考虑采用 SPI 信道替代原有的蓝牙信道，然而相比于蓝牙——串 又信道，SPI 的开发不论是在上位机方面还是在 FPGA 方面均比较复 杂，因此不一定可以完成。
综合以上三种通信机制的优缺点，我们选择蓝牙信道作为通信手段。

## 三、方案比较和选择

- 主控元件
- 通信机制
- 供电方式
- 摄像头数据传输技术
- 车辆位置信息处理方式
- 其他注意事项

## 供电方式

- 5V@1.5A——向FPGA和舵机供电
- 3.3V@1.5A——向外设供电
- 7.2V@40A——向电机供电，接受PWM

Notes: 首先通过查阅可能使用到的外设的技术手册，我们大概确定了供电需求为
• 5V@1.5A
• 3.3V@1.5A • 7.2V@40A
其中 5V@1.5A 负责向 FPGA 5V@1A 以及舵机供电，3.3V 电源负责向外 设供电，例如我们采用的摄像头 OV7670 采用的供电电压为 3.3V@100mA。 7.2V@40A 电源负责向电机供电，并应接受 PWM 调制来控制电机转速。
2 方案比较与选择 5
通过查阅资料我们发现，供电的难点在 7.2V@40A 电源，而 5V@1.5A 电源和 3.3V@1.5A 电源均可以使用实验室提供的 TPS54160 SMT 芯片完 成设计，这一部分内容将在后面基于 Webench 的仿真实现上面进行说明。 7.2V@40A 电源的电流限额主要受到电机供电电流要求影响，从实验室提供 的数据手册我们可以发现，电机的空载电流 2.4A，最高效率电流 11A，堵 转电流 52.8A，根据网上查阅的相关资料，电机的限流应当是最高效率电流 的约 4 倍，因此设计 7.2V@40A 电源负责向电机供电。
这里讨论 7.2V@40A 电源的设计问题。因为需要接受 PWM 信号调制，
因 此 我 们 采 用 了
H 桥的电路原理图如图 2所示。
Q1Q̃4 可以由处于饱和状态的三极
管或开关状态的 MOS 管组成 J1 和
J2 分别接入前一级驱动电路产生的
两个反相 PWM，设某时刻 J1 为高
电平，则 Q3 导通，Q1 截止;由于
反相，J2 为低电平，Q2 导通，Q4 截
止，电流由通过 Q2，经负载，再经
过 Q3 流入地。同理，当某时刻 J1
为低电平时，Q1,Q4 导通，Q2,Q3 截止，电流依次经 Q1,R1,Q4 流入地。综 上，任意时刻有且只有一个对角线上的两个 MOS 管是导通的。
对于电机，我们可以设定刹车模式，即可以通过与上述方法类似的方法 将电机两脚短路，使得电机迅速产生电磁制动实现刹车效果
通过搜索符合要求的元件，我们发现合理的解决方案为 bts7960/7961 芯片和自行搭建 H 桥两种方案。
bts7960/7961 芯片是接受 5VPWM 信号调制的，输入电压 5.5V 至 27V@43A 的半 H 桥电路，采用 SMT 封装，输出电流符合要求。然而，由 于我们电机的额定输入电压为 7.2V，经过对电机的初步调试我们可以发现 电机在 7.2V 输入电压下的转速非常高，导致速度不能得到控制，经过进一 步的实验我们发现，在低于数据手册上提供的 5.4V 供电的情况下，电机的 转速可以保证一个理想的状态，因此可以初步得到结论即 PWM 信号的占 空比不可过高。
而自行搭建 H 桥，因为工艺比较复杂，同时在网上找不到合适的大功 率 MOS 管供应商，因此我们放弃了这个方案。

## 三、方案比较和选择

- 主控元件
- 通信机制
- 供电方式
- 摄像头数据传输技术
- 车辆位置信息处理方式
- 其他注意事项

## 摄像头数据传输技术

- OV7670
  - CMOS图像传感器，输出时钟约8MHz
- 直接采集
  - IO速度不足
  - 降低CMOS输出速度，配置复杂，图像可能失真
- DMA
  - 在FPGA上效果不明显
- FIFO模块采集
  - 不需要高速IO
  - 开发较简单


√

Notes: 我们采用的 OV7670 摄像头，可以输出 25fps 640*480 VGA 格式的 RGB 三 色图像，输出采用 8 线同步并行传送因此输出时钟速度可以达到 25 ∗ 640 ∗ 480 ≈ 8MHz。收到蓝牙信道是串行接又的原因，蓝牙信道的速度必须达到 8MB/s，这是一般蓝牙系统很难做到的。因此不论是 FPGA 读取信息还是 蓝牙传输信息的速度，均不如摄像头采集数据的速度，需要找到合理的解决 方式。
经过我们查阅相关资料发现，OV7670 的传输方式有如下三种形式: • MCU/FPGA 直接采集:
如图 3所示，这种方法是最简
单，最直接，但也是最不好实
现的方法，以 MCU 为例，多
数的 CMOS 芯片(如 ov7670)
的时钟速度可高达 24M，一
般 MCU 的 IO 端又速度根
本不可能达到，所以需要高速
MCU。这对多数用户来讲有些
不现实。但也不是完全没有办
法在低速上实现采集，方法也
很简单，那么就是降低 CMOS
的输出速度，不过这需要靠外
部的晶振和内部的 PLL 电路
以及像素时钟速度，帧速等多
个寄存器共同设置，并且要和
MCU 的 IO 速度匹配才可实 现。但这么做将带来巨大的寄存器设置工作量并导致硬件图像的采集 速度可能下降到 0.5 帧以下，同时带来图像失真的可能。
• DMA 方式
这种方式主要用于 MCU 中，FPGA 中这种方式效果不明显，DMA 控 制器使得数据可以绕过 CPU 直接进入内存，但是在 FPGA 中，同时 受到串又通信速度的影响，这种方式效果也不是很明显。
• FIFO 模块采集
如图 4，用户只需要按上述时序图控制相关的几个控制引脚即可，可
Fig. 3: MCU/FPGA 直接采集
Fig. 4: FIFO 采集
2 方案比较与选择 7
以很方便的使用在低速 MCU 上，另外一个好处是，可以直接 IO 又读 取数据，读出的数据可以直接送屏，也可以经过 MCU 简单处理;当 然也可以不经过 MCU，直接送到屏等外围器件使用。对于 FPGA，以 及速度相对较低的串又单元，使用 FIFO 也能很大程度的解决速度不 同步的问题。

## 三、方案比较和选择

- 主控元件
- 通信机制
- 供电方式
- 摄像头数据传输技术
- 车辆位置信息处理方式
- 其他注意事项

## 车辆位置信息处理方式

- IMU
  - 通过加速度计和陀螺仪直接读取
  - 加速度计易受颠簸、碰撞、刹车等造成脉冲影响，积分计算误差大
  - 陀螺仪存在温漂和零点波动，积分计算误差大
- 磁场计
  - 一般误差较小，但受电机产生磁场影响，此方案基本无效
- 码盘
  - 使用光电传感器测量车轮转速，解算后得到具体位置，较准确
  - 难点在于码盘的安装和对小车的建模

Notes: 为了进一步增强 3D 建模的精度，我们希望能够采集车辆的位置信息和角度 信息。由于摄像头和车辆是相对固定的，这样也就获得了摄像头的位置信息 和角度信息。
根据我们查阅到的资料，车辆的位置信息和角度信息有几种不同的获 取方式，如下所示。
惯性测量单元(IMU)模块
通过加速度计和陀螺仪的信息，可以直接读取车辆的加速度和角度。 经过积分之后可以得到车辆的速度信息和角度信息，这种方法最简单， 但是误差最大，加速度计易受到颠簸，碰撞，刹车等造成的脉冲影响， 并进一步影响积分的准确性。角速度计(陀螺仪)具有一般性的零点 迁移问题，这包括动态的零点波动和静态的温漂。经过积分会导致角 度信息相当不准确。这种方法只能作为一种简单的参考，实用时必须 加以处理。
磁场计
通过对地磁角度的测定，可以直接获取车辆的角度，并通过加速度计 等方式获得车辆的速度，这种方式误差相对前一种较小，但是受外界 磁场的影响比较严重，尤其是当存在 10A 绕组的电机驱动时，这种方 法可以认为无效。
码盘
这种方法通过测量车辆四轮的转速经过解算得到车辆的具体位置，相 比于之前几种方式，这种方式依赖于更加准确的光电传感器，因此得 到的值也相对比较准确，这种方法的难点在于必须对车辆的刚性模型 进行建模，同时安装码盘也是一个硬件上的难点。
综合提到的几种方法，我们计划采取 IMU+ 信号处理 + 码盘解算几种方式 得到车辆的具体位置，希望通过反馈等方式希望得到更准确的车辆控制。

## 三、方案比较和选择

- 主控元件
- 通信机制
- 供电方式
- 摄像头数据传输技术
- 车辆位置信息处理方式
- 其他注意事项

## 其他注意事项

- 采用74HC244作为电源接口的辅助电路
- 摄像头模块采用SCCB通信协议，其中有两个OC门需要外接上拉电阻，需要在设计PCB时尽量考虑周全
- 获取小车位置信息时涉及浮点数，而FPGA处理浮点数较困难，选用NI myRIO进行开发

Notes: 通过查阅给定的技术手册我们发现 FPGA 输入电流 1A，标准的输出电压为 3.3V，而不论是电机驱动的 PWM 还是舵机驱动的 PWM 均为 5V，这中间 需要设计适当的接又电路，同时，由于工程量比较大，担心 FPGA 会出现 总线电流过大或无法驱动相关接又电路的情况，因此我们采用了 74HC244 芯片作为接又的辅助电路，74HC244 是一款高速 CMOS 驱动芯片，通过 HC244 我们可以顺利的将 3.3V 输出转化为 5V，并提升驱动能力。
通过对摄像头模块 OV7670 的数据手册的学习，我们了解到 OV7670 初始化采用的是 SCCB 通信协议，SCCB(Serial Camera Control Bus)是 和 I2C 相同的一个协议。SIO_C 和 SIO_D 分别为 SCCB 总线的时钟线和 数据线，为了方面对多个设备进行控制，OV 的 SCCB 两个端又采用的均是 OC 门输出，需要上拉 4.7k 电阻实现输出高低电平，这些需要在设计 PCB 的时候尽可能的考虑到并保证接线的稳定性和摄像头位置的稳定性。
在设计对车辆相对位置进行测量的过程中，考虑到 FPGA 在解算浮 点数方面比较难以开发，我们选用了 NI myRIO 进行解算和控制，并采用 myRIO 自带的 WiFi 进行相关数据的回传。
NI myRIO 是 NI 针对教学和学生创新应用而最新推出的嵌入式系统 开发平台。NI myRIO 内嵌 Xilinx Zynq 芯片，使学生可以利用双核 ARM Cortex-A9 的实时性能以及 Xilinx FPGA 可定制化 I/O，学习从简单嵌入 式系统开发到具有一定复杂度的系统设计，采用 LabView 语言进行可视化 编程。通过 myRIO 可以大幅简化控制算法如 PID 的调试过程，显著降低 开发难度，加速开发进度。

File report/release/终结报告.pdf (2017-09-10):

### 电子技术课程设计

# 基于受控无人车的场地探测和 3D 重建系统

# 终结报告

## 张蔚桐 2015011493 自 55 陈 崴 2015011481 自 55

目录

1

2

1 选题背景及课题简介 | 3

### 1 选题背景及课题简介

根据《智能交通》和《智能家居》的课题方向，我们将选题定位为基于受控 无人车的场地探测和 3D 重建系统。


Fig. 1: “蝎形”（”scorpion”）机器人 行进在福岛核电站 2 号反应堆
内

目前，受控无人车，即对无人车
发送指令控制无人车的技术已经有
了很多现实生活中的应用。然而，这
种受控无人车要求控制者能够看到
无人车的运动状态，并对无人车进
行控制。这样不方便无人车进一步
进行无人作业。例如，在地震灾区倒
塌的房间中，控制人员无法看到无人
车的具体位置，这就需要无人车对周
边环境数据进行采集，方便控制人员
进行进一步的控制。另外，通过加装
场地检测装置，无人车或机器人可
以到很多危险场合进行作业和信息
的采集。例如，2011 年日本福岛核
泄漏之后，东电公司曾派遣如图 1所
示的机器人到反应堆内调查事故情况。通过加装摄像头和辐射监测设备，机 器人可以在人类无法承受的辐射量内进行高强度监测作业。
另外，目前 3D 检测和建模技术方兴未艾。利用无人机等设备对建筑物 外表面进行 3D 检测建模的技术已经实现。计算机视觉领域内，SfM(Shape from Motion) 等基于单目摄像机的 3D 重建技术已经相对比较成熟，因此， 周边技术的成熟为我们的设计提供了相当的基础。同时，我们也考虑采集小 车的位置信息，一方面，对于控制人员来说，了解小车的行进路线（相对位 置）也是一个很重要的信息点，另外一方面，根据计算机的相关知识，我们 也可以知道获取准确的拍摄角度和拍摄位置可以更好的加大 3D 重建的精 度，而这方面的应用和算法据我们所查阅的资料来看相对较少，可以进行进 一步的创新。
因此我们将选题定位基于受控无人车的场地探测和 3D 重建系统，目标 是通过控制无人车的行为，完成对场地内图像信息的采集，并在合适的情况 下允许上位机进行 3D 重建，完成对场景 3D 状态的描述工作。根据时间限 制和具体的完成情况，我们将整个项目分为如下几个部分进行。
1. 第一部分
- 基本的电源管理和小车运动控制

2 方案比较与选择 | 4
- 在上位机控制下小车完成相关运动
- 小车安装摄像头，将图像回传上位机
2. 第二部分
- 图像实时回传
- 小车完成相对位置信息的记录和回传
- 利用位置信息进行二维地图的展示工作
3. 第三部分
- 将上位机应用部署到移动平台
- 小车安装避障系统，并可以自动运行
- 三维重建，同时利用位置信息

从上面我们可以看出整个工程量较大，受到两周的开发时间的限制可能不一 定全部完成，剩余工程可以作为参加挑战杯等进一步开发项目的发展方向。

### 1.1 具体完成情况

这一节总结一下提到的项目内容的完成情况
经过两周的具体调试，我们实现了第一部分的所有具体要求，包括小车 的驱动模块，摄像头的安装和测试，蓝牙模块通信的测试等，并完成了整个 项目的整合。但是由于蓝牙速度较慢，经过了长时间的调试，我们仍然不能 实现图像的实时回传，同时，由于图像数据量较大，回传图像对蓝牙压力也 比较大导致蓝牙模块并不是很稳定。虽然如此，整个项目的工作量，完成 度和可展示性还是非常理想的，尤其是对基于 FPGA 对裸 CMOS 摄像头 OV7670 的封装等为代表的工作花费了我们大量的心血，总结起来还是比较 满意的。

### 2 方案比较与选择

### 2.1 主控元件的选择

首先我们考虑主控元件的选择，根据我们的技术水平和课题的情况，可供选 择的主控芯片为 MCU （单片机）和 FPGA。相比 FPGA，MCU 具有开发 相对简单的优势，以串口通信协议为例，大部分 MCU 的系统库中均已经封 装了串口通信协议，而 FPGA 相对更接近底层，因此需要自行完成相关的 通信协议的封装，这将消耗大量的时间和精力。

2 方案比较与选择 | 5

然而，相比于 MCU，FPGA 在速度和并行性方面有着很大的优势。根 据我们查阅的资料，以 STMF103 为例，其时钟速度可以达到 72MHz，然而 由于串行执行的原因，IO 速度相对于 FPGA 较低；对比我们使用的 Xilinx FPGA，其时钟速度可以达到 100MHz，同时高度并行使得模块之间互相不 干扰，保证了 IO 速度等要求。
因此，考虑到性能要求以及课程需要，我们在硬件方面采用了 FPGA 作为主控进行开发。

### 2.2 通信机制的选择

根据查阅的资料，可供选择的无线通信机制有如下三种：

1. WiFi 信道

这种通信机制需要将 WiFi 模块植入硬件，使得小车可以联网传输信 息。上位机或移动平台使用 WiFi 下载信息。这种方式的优势一方面 是信息传输距离较远，在一个路由器覆盖的范围内，信息均可以被传 输。另一方面可拓展性也比较强，如果设计了合理的联网方式，将进 一步解除距离限制，通过将信息上传到云空间，用户可以在任何联网 的地区完成信息的收取和对小车的控制。

这种通信机制的缺点是过于复杂，尤其是使用 FPGA 进行开发的情况 下，网络通信协议将带来更大的开发时间消耗，不适用于本课程的短 期开发。

2. 蓝牙信道

这种通信机制利用蓝牙模块，蓝牙模块已经将蓝牙信道封装成串口的 形式，从很大程度上方便了开发。同时，通过对电脑，移动设备上的蓝 牙模块进行开发，用户可以不依赖于第三方设备（如路由器）和小车 进行通信。虽然通信速度上相比 WiFi 也有一定的损失，并且通信距 离受到明显限制，但相比于 WiFi 模块而言，其功耗更小。

3. SPI 信道

后期的开发表明，蓝牙的速度并不能保证摄像头传输的实时性，因此 后期考虑采用 SPI 信道替代原有的蓝牙信道，然而相比于蓝牙——串 口信道，SPI 的开发不论是在上位机方面还是在 FPGA 方面均比较复 杂，因此不一定可以完成。

综合以上三种通信机制的优缺点，我们选择蓝牙信道作为通信手段。

2 方案比较与选择 | 6

### 2.3 供电方式的选择

首先通过查阅可能使用到的外设的技术手册，我们大概确定了供电需求为

- 5V@1.5A
- 3.3V@1.5A
- 7.2V@40A

其中 5V@1.5A 负责向 FPGA 5V@1A 以及舵机供电，3.3V 电源负责向外 设供电，例如我们采用的摄像头 OV7670 采用的供电电压为 3.3V@100mA。 7.2V@40A 电源负责向电机供电，并应接受 PWM 调制来控制电机转速。 通过查阅资料我们发现，供电的难点在 7.2V@40A 电源，而 5V@1.5A 电源和 3.3V@1.5A 电源均可以使用实验室提供的 TPS54160 SMT 芯片完 成设计，这一部分内容将在后面基于 Webench 的仿真实现上面进行说明。 7.2V@40A 电源的电流限额主要受到电机供电电流要求影响，从实验室提供 的数据手册我们可以发现，电机的空载电流 2.4A，最高效率电流 11A，堵 转电流 52.8A，根据网上查阅的相关资料，电机的限流应当是最高效率电流 的约 4 倍，因此设计 7.2V@40A 电源负责向电机供电。
这里讨论 7.2V@40A 电源的设计问题。因为需要接受 PWM 信号调制，
因 | 此 | 我 | 们 | 采 | 用 | 了 | H | 桥 | 进 | 行 | 设 | 计。


Fig. 2: H 桥的电路原理图

H 桥的电路原理图如图2所示。Q1Q̃4
可以由处于饱和状态的三极管或开
关状态的 MOS 管组成 J1 和 J2 分
别接入前一级驱动电路产生的两个
反相 PWM，设某时刻 J1 为高电平，
则 Q3 导通，Q1 截止；由于反相，J2
为低电平，Q2 导通，Q4 截止，电流
由通过 Q2，经负载，再经过 Q3 流
入地。同理，当某时刻 J1 为低电平
时，Q1,Q4 导通，Q2,Q3 截止，电流依次经 Q1,R1,Q4 流入地。综上，任意 时刻有且只有一个对角线上的两个 MOS 管是导通的。 对于电机，我们可以设定刹车模式，即可以通过与上述方法类似的方法 将电机两脚短路，使得电机迅速产生电磁制动实现刹车效果 通过搜索符合要求的元件，我们发现合理的解决方案为 bts7960/7961 芯片和自行搭建 H 桥两种方案。
bts7960/7961 芯片是接受 5VPWM 信号调制的，输入电压 5.5V 至 27V@43A 的半 H 桥电路，采用 SMT 封装，输出电流符合要求。然而，由

2 方案比较与选择 | 7

于我们电机的额定输入电压为 7.2V，经过对电机的初步调试我们可以发现 电机在 7.2V 输入电压下的转速非常高，导致速度不能得到控制，经过进一 步的实验我们发现，在低于数据手册上提供的 5.4V 供电的情况下，电机的 转速可以保证一个理想的状态，因此可以初步得到结论即 PWM 信号的占 空比不可过高。
而自行搭建 H 桥，因为工艺比较复杂，同时在网上找不到合适的大功 率 MOS 管供应商，因此我们放弃了这个方案。

### 2.4 摄像头数据传输技术的选择

我们采用的 OV7670 摄像头，可以输出 25fps 640*480 VGA 格式的 RGB 三 色图像，输出采用 8 线同步并行传送因此输出时钟速度可以达到 25 ∗ 640 ∗ 480 ≈ 8MHz。收到蓝牙信道是串行接口的原因，蓝牙信道的速度必须达到 8MB/s，这是一般蓝牙系统很难做到的。因此不论是 FPGA 读取信息还是 蓝牙传输信息的速度，均不如摄像头采集数据的速度，需要找到合理的解决 方式。
经过我们查阅相关资料发现，OV7670 的传输方式有如下三种形式：


Fig. 3: MCU/FPGA 直接采集


Fig. 4: FIFO 采集

- MCU/FPGA 直接采集：

如图3所示，这种方法是最简单，
最直接，但也是最不好实现的
方法，以 MCU 为例，多数的
CMOS 芯片（如 OV7670）的时
钟速度可高达 24M，一般 MCU
的 IO 端口速度根本不可能达
到，所以需要高速 MCU。这对
多数用户来讲有些不现实。但
也不是完全没有办法在低速上
实现采集，方法也很简单，那么
就是降低 CMOS 的输出速度，
不过这需要靠外部的晶振和内
部的 PLL 电路以及像素时钟
速度，帧速等多个寄存器共同
设置，并且要和 MCU 的 IO 速
度匹配才可实现。但这么做将
带来巨大的寄存器设置工作量并导致硬件图像的采集速度可能下降到

2 方案比较与选择 | 8

0.5 帧以下，同时带来图像失真的可能。

- DMA 方式

这种方式主要用于 MCU 中，FPGA 中这种方式效果不明显，DMA 控 制器使得数据可以绕过 CPU 直接进入内存，但是在 FPGA 中，同时 受到串口通信速度的影响，这种方式效果也不是很明显。

- FIFO 模块采集

如图4，用户只需要按上述时序图控制相关的几个控制引脚即可，可以 很方便的使用在低速 MCU 上，另外一个好处是，可以直接 IO 口读 取数据，读出的数据可以直接送屏，也可以经过 MCU 简单处理；当 然也可以不经过 MCU，直接送到屏等外围器件使用。对于 FPGA，以 及速度相对较低的串口单元，使用 FIFO 也能很大程度的解决速度不 同步的问题。

### 2.5 车辆位置角度信息处理方式的选择

为了进一步增强 3D 建模的精度，我们希望能够采集车辆的位置信息和角度 信息。由于摄像头和车辆是相对固定的，这样也就获得了摄像头的位置信息 和角度信息。
根据我们查阅到的资料，车辆的位置信息和角度信息有几种不同的获取 方式，如下所示。
- 惯性测量单元（IMU）模块

通过加速度计和陀螺仪的信息，可以直接读取车辆的加速度和角度。 经过积分之后可以得到车辆的速度信息和角度信息，这种方法最简单， 但是误差最大，加速度计易受到颠簸，碰撞，刹车等造成的脉冲影响， 并进一步影响积分的准确性。角速度计（陀螺仪）具有一般性的零点 迁移问题，这包括动态的零点波动和静态的温漂。经过积分会导致角 度信息相当不准确。这种方法只能作为一种简单的参考，实用时必须 加以处理。

- 磁场计

通过对地磁角度的测定，可以直接获取车辆的角度，并通过加速度计 等方式获得车辆的速度，这种方式误差相对前一种较小，但是受外界 磁场的影响比较严重，尤其是当存在 10A 绕组的电机驱动时，这种方 法可以认为无效。

2 方案比较与选择 | 9
- 码盘

这种方法通过测量车辆四轮的转速经过解算得到车辆的具体位置，相 比于之前几种方式，这种方式依赖于更加准确的光电传感器，因此得 到的值也相对比较准确，这种方法的难点在于必须对车辆的刚性模型 进行建模，同时安装码盘也是一个硬件上的难点。

综合提到的几种方法，我们计划采取 IMU+ 信号处理 + 码盘解算几种方式 得到车辆的具体位置，希望通过反馈等方式希望得到更准确的车辆控制。

### 2.6 其他注意事项

在设计对车辆相对位置进行测量的过程中，考虑到 FPGA 在解算浮点数方 面比较难以开发，我们选用了 NI myRIO 进行解算和控制，并采用 myRIO 自带的 WiFi 进行相关数据的回传。
NI myRIO 是 NI 针对教学和学生创新应用而最新推出的嵌入式系统 开发平台。NI myRIO 内嵌 Xilinx Zynq 芯片，使学生可以利用双核 ARM Cortex-A9 的实时性能以及 Xilinx FPGA 可定制化 I/O，学习从简单嵌入 式系统开发到具有一定复杂度的系统设计，采用 LabView 语言进行可视化 编程。通过 myRIO 可以大幅简化控制算法如 PID 的调试过程，显著降低 开发难度，加速开发进度。

### 2.7 实际项目的修正和改动

实际项目进行过程中，我们尽可能的对蓝牙的速度进行了利用，然而由于 蓝牙速度受限，导致实际上图像回传不能实时化，并且对蓝牙通信速度上限 的冲击导致蓝牙出现不稳定情况。在这种情况下，我们希望采用 SPI-WiFi-TCP 通信协议，然而 TCP 协议封装复杂，经过我们查阅相关资料，TCP 的 引脚数量甚至超过了我们使用的 FPGA 的全部可控引脚数量，‘同时 TCP 通信机制也比较复杂，会对是 FPGA 层面的封装还是上位机的编写带来巨 大的困难，因此我们最终放弃了这种思路。
同时，对于陀螺仪和测速方面，由于我们使用的 FPGA 引脚已经全部被 占用，导致基于 FPGA 的相关开发变得不现实，因此我们选用了 NI myRIO 进行相关的开发，并完成了陀螺仪模块。对于测速模块，我们发现不论是车 轮还是电机均很难安装码盘，因此我们采用了对车轮进行标注并利用红外 进行测速，并基于 myRIO 调通了相关的功能，然而由于我们设计的车辆行 驶速度偏慢，因此相关的测速变得没有实际意义，最终我们放弃了这个模块 的整合工作。

3 基于 FPGA 的数字系统框图 | 10


Fig. 5: 基于 FPGA 的数字系统框图

### 3 基于 FPGA 的数字系统框图

如图5所示，左侧为封装的顶层模块，从右侧可以看出共分为 8 个子模块。

- CLK_GEN

该模块对 100MHz 系统时钟分频，输出 4 个时钟分别供串口、舵机、 电机、摄像头使用。

- UART_RX

蓝牙串口接收模块，RX 为数据线，每从上位机接收一个码元即触发 finish 信号，并将数据存在 data 寄存器供其他模块使用。同时内部还 提供了一个 error 接口，接收数据发生错误时触发。

- UART_TX

蓝牙串口发送模块，TX 为数据线，当触发 start 信号后，将 data 寄 存器中的内容发送给上位机，发送完成后会得到一个 finish 信号反馈。

- SERVO

舵机控制模块，从串口接收转向控制指令，输出舵机 PWM 信号。

4 传感器/执行机构接口电路图 | 11
- MOTOR

电机控制模块，同样从串口接收指令，输出电机使能和 PWM 信号。

- OV_INIT

摄像头初始化模块，SCL 和 SDA 为 SCCB 协议的时钟线和数据线， 初始化前 initialized_flag 为低电平，OV_STORE 和 OV_READ 处 于失能状态，初始化完成后拉高 initialized_flag，摄像头便可正常工 作。

- OV_STORE

将摄像头采集到的图像存储于 FIFO 中，存储完成一帧后触发 new_frame_flag 信号，等待 FPGA 读取图像结束后才继续采集下一帧。

- OV_READ

从 FIFO 中读取一帧图像，并存储在 frame_data 寄存器中，读取完 成后触发两个信号，一个是 frame_read_flag，通知摄像头可以继续采 集下一帧图像，另一个是 new_frame_data_flag，通知顶层模块将读 取到的数据发送给上位机。

### 4 传感器/执行机构接口电路图

### 4.1 传感器电路

### 4.1.1 数字接口电路


Fig. 6: OV 上拉电阻和转接电路

这部分主要是完成数字模块之间的
接口电路，由于各个数字模块已经
将输出电平统一标准化为 TTL 电
平，因此这部分的关键主要是接口
通信协议的实现，主要有 FPGA 方
面实现了 SCCB 接口通信协议，串
口通信协议，摄像头数据读取协议
等。另外，SIO_C 和 SIO_D 分别
为 SCCB 总线的时钟线和数据线，为
了方面对多个设备进行控制，OV 的
SCCB 两个端口采用的均是 OC 门
输出，需要上拉 4.7k 电阻实现输出
高低电平，这些需要在设计 PCB 的

4 传感器/执行机构接口电路图 | 12

时候尽可能的考虑到并保证接线的稳定性和摄像头位置的稳定性，因此需 要在 PCB 上统一制作并提供对 FPGA 的简单的接线电路，这部分的电路 可以如图6所示。


Fig. 7: 74HC244 驱动器电路

另一部分的接口电路问题是
3.3V 电平标准和 5V 电平不匹配的
问题以及同时设计到的 FPGA 驱
动能力不足的问题通过查阅给定的
技术手册我们发现 FPGA 输入电流
1A，标准的输出电压为 3.3V，而不
论是电机驱动的 PWM 还是舵机驱
动的 PWM 均为 5V，这中间需要设
计适当的接口电路，同时，由于工程
量比较大，担心 FPGA 会出现总线
电流过大或无法驱动相关接口电路
的情况，因此我们采用了 74HC244
芯片作为接口的辅助电路，74HC244
是一款高速 CMOS 驱动芯片，支持
三态门使能，通过 HC244 我们可以
顺利的将 3.3V 输出转化为 5V，并提升驱动能力。根据 74HC244 的接线要 求，我们在输入端接入下拉电阻 1k 实现相关功能。这部分的电路有如图7所 示。同时我们将剩下的 74HC244 引脚同样通过排针引出，留待之后使用。

### 4.1.2 模拟接口电路


Fig. 8: ENC-03 模块外部电路图

我 们 计 划 采 用 输 出 模 拟 电 压 的
ENC-03 陀螺仪，这是是一种应用
科氏力原理的角速度传感器，陀螺
输出一个和角速度成正比的模拟电
压信号。通过积分电路可以得到相
关的角度等。根据 ENC-03 技术手
册，我们设计输出放大电路如图8所
示，整个电路由两个滤波器组成，左
侧为低通滤波器，用于滤除传感器高
频噪声，右侧为高通滤波-放大电路，用于放大电压信号和滤除低频温漂。 进一步，我们搭建基本积分电路可以得到角度信息，两个信息通过 AD 模块可以返回给主控设备。由于我们计划采用 myRIO 进行位置信息的测 量，因此这部分可以直接使用 LabVIEW 语言在 myRIO 上完成，就没有设

5 基于 Webench 的电源电路仿真 | 13

计电路的必要了。

### 4.2 执行接口电路

这部分主要描述的是对电机和舵机的驱动电路
对于舵机驱动，单片机输出高电平为 3.3V 的 PWM 脉冲，经过前文提 到过的 74HC 模块转 5V 驱动舵机旋转。


Fig. 9: 电机驱动电路

对于电机驱动，我们使用 BTN7970
模块，如图9所示。这里为了方便
后文叙述，两片 IN 引脚被命名为
IN1，IN2，两片 INT 引脚被命名为
INT1,INT2。我们将 INT1,INT2 短
接并输入 PWM 波形控制电机转动
速度。将 IN1，IN2 分别接高低电平
控制电机正转反转。例如 {INT1 =
0,INT2 = 1} 代表电机正转，{INT1
= 1, INT2 = 0} 代表电机反转。当
{INT1 = 0,INT2 = 0} 时，H 桥全 部关断，表示不控制电机转动。当
{INT1 = 1,INT2 = 1} 时，H 桥下 部导通，电机两端短接，使得电机的
机械能通过电磁感应和短路线迅速
释放，实现刹车功能。BTN 相关引
脚仍为 5V 接线，因此使用 74HC244 完成相关的电平转换和放大工作。

### 5 基于 Webench 的电源电路仿真

WEBENCH 是 TI 公司提供的设计环境，通过软件工具提供定制电源等的 设计，通过使用 WEBENCH 可以提升设计效率。整体的设计思路如下：

- 输入电压的确定

我们将电池断开，测量电压约为 8.2V，将电池直接接电机，并在电机 上施加比较大的阻力，发现电源电压约为 7V，因此我们设计电源时考 虑输入电压为 6V9̃V 即可满足需求。

- 输出电压的确定

由表1所示，我们需要向 FPGA 提供 5V 外接电源，对舵机提供 5V 外 接电源，对外设提供 3.3V 外接电源，因此设计输出电压为 5V，3.3V。

5 基于 Webench 的电源电路仿真 | 14


- 输出电流的确定

首先根据实验室提供的 TI 样片，我们选择了 TI TPS54160 降压模块， TPS54160 器件是一款带有集成型高侧 MOSFET 的 60V,1.5A 的降压 稳压器。电流模式控制提供了简单外部补偿和灵活组件选择，功耗较 小。

根据 TPS54160 的输出电流，我们限制电源输出电流为 1.5A。同时查 阅技术手册可以得到主要的部件的供电信息如表1所示, 总计需要输出 电流 5V@2A,3.3V@500mA，因此需要设计两路 5V 供电电源，其中一 路 FPGA 自用（包括驱动器 74HC244），一路给舵机/外设使用。

因此，进入 WEBENCH 中提供需求的输入，输出信息，选择器件为 TPS54160， 可以得到元件的原理图。通过调整原理图上的元件的值的信息，可以选用已 有阻值的元件进行仿真，最终确定的电路原理图和响应时间仿真和稳态仿 真如下面几张图所示。两个电路结构相同，相关参数差别如表3所示。整理 仿真结果如表2所示。可以看出电源的性能效果还是比较理想的，可以进行 实际电路的搭建。

Tab. 1: 主要部件供电信息
部件 | 电压 | 电流
FPGA | 5V | 1A
舵机 | 5V | 800mA
74HC244 | 5V | 100mA
蓝牙模块 | 5V | 100mA
OV7670 | 3.3V | 200mA

Tab. 2: 仿真主要性能指标
参数 | 3.3V 电源 | 5V 电源
稳态电压平均值 | 3.435V | 5.326V
稳态电压峰峰值 | 3.648mV | 2.465mV
启动时间 | 1.368ms | 2.379ms
电感电流峰值 | 1.245A | 1.753A

5 基于 Webench 的电源电路仿真 | 15

Tab. 3: 元件参数信息
元件名 | 类别/单位 | 3.3V 电源 | 5V 电源
Cin | 电解电容/µF | 470 | 470
Rent | 定值电阻/kΩ | 110 | 110
RenB | 定值电阻/kΩ | 33 | 33
Ccomp | 独石电容/nF | 1 | 1
Ccomp2 | 独石电容/pF | 10 | 10
Rcomp | 定值电阻/kΩ | 33 | 56
Css | 独石电容/nF | 6.8 | 6.8
Rt | 定值电阻/kΩ | 110 | 110
Cboot | 独石电容/nF | 100 | 100
D1 | 肖特基二极管/型号 | SS24FL | SS24FL
L1 | 定值电感/µH | 100 | 100
Rfbt | 定值电阻/kΩ | 33 | 56
Rfbb | 定值电阻/kΩ | 10 | 10
Cout | 电解电容/µF | 470 | 470


Fig. 10: 5V 电源启动情况


Fig. 11: 5V 电源稳态情况


Fig. 12: 3.3V 电源启动情况


Fig. 13: 3.3V 电源稳态情况

6 PCB 的设计制作 | 16

Tab. 4: PCB 线宽和电流的关系
电流 (A) | 线宽 (mm) | 电流 (A) | 线宽 (mm)
6.0 | 2.5 | 5.1 | 2.0
4.2 | 1.5 | 3.6 | 1.2
3.3 | 1.0 | 2.8 | 0.8
2.3 | 0.6 | 2 | 0.5
1.7 | 0.4 | 1.3 | 0.3
0.9 | 0.2 | 0.7 | 0.15


Fig. 14: PCB 版效果图

### 6 PCB 的设计制作

完成了电源模块的仿真之后就可以开始着手进行 PCB 的设计制作了，在设 计制作的过程中，由于考虑到手工焊接的困难，因此尽可能多的选用了插接 件代替 SMT 封装元件，如电阻，电容等，同时，根据走线可能涉及的电流 大小如图4所示，我们设计走线宽度为

- 对 BTN 驱动板，走线 40mil(1mm)，对应电流 3A 左右
- 对电源管理模块，走线 15mil(0.4mm)，引脚处走线 10mil(0.25mm)，对 应电流 1.5A 左右

同时对大电流部分加焊锡保护走线，防止过热。整版 PCB 单面布线，背面 加装散热片，保证散热顺畅并注意 IC 散热引脚接触良好。同时考虑接线端 子，IC 等的位置关系，充分考虑日后安装，打孔位置，保证接线顺利同时 散热合理。PCB 如图14所示。

7 课题开发与调试中出现的问题分析 | 17

### 7 课题开发与调试中出现的问题分析

### 7.1 数字电路部分

数电部分完全使用 FPGA 进行开发，遇到的困难几乎都来自 ov7670 图像 传感器模块。
首先，图像传感器在工作前需要先进行寄存器初始化配置，读写寄存器 使用的是 SCCB 协议。一开始调试时，待写入的寄存器的地址和内容都存 放在文本文件中，且因为数据是串行写入，各个寄存器的初始化是顺序执行 的，所以初始化语句都写在 initial 块中，又由于每次读或写一个寄存器都 需要 SCCB 协议中的起始、应答、结束等信号，这就会产生大量对时钟线 重复的操作，为了使代码看起来更简洁，这些相同的操作都封装成了 task。 这样一来，尽管在仿真测试时代码都正常运行，但电路却是不可综合的。 最后，解决这些问题的方式是重写代码，将各寄存器地址和内容都以常 量形式存在 FPGA 中，以 FSM 状态的跳转模拟各语句的顺序执行，大量 相同的操作也只能重复相同的代码。其中还发现寄存器配置需要一定的反 应时间，因此每写入一字节后都加入几毫秒的延时。
图像传感器的初始化只进行一次，而图像的采集和读取是无限循环的， 且必须在初始化完成后才能进行，所以使用了一个全局的信号来判断初始化 是否完成。前文已经分析过使用 FIFO 模块采集图像的好处，但是在我们查 阅到的资料中，绝大部分不带 FIFO 的传感器封装成 18 个引脚，带 FIFO 的传感器封装成 22 个引脚，而为了节省 FPGA 的 IO，我们选购的传感器 是带 FIFO 模块且封装为 18 个引脚的，这种封装的资料几乎找不到，开发 完全没有前车之鉴，只能依赖于 ov 公司和 FIFO 芯片的数据手册。这些数 据手册中提供的都是各 IC 引脚的时序，而封装后外部引脚的时序只能靠分 析和推测。在硬件调试时，我们合理地使用 FPGA 上的 LED 进行辅助调 试，通过 LED 的状态来分析电路状态，从而找出代码中的错误，大大节省 了开发时间。
通过蓝牙串口模块回传数据时，理论上传输速率可以达到 1.3 秒每帧， 但实际测试中发现，如果以这么高的速率发送数据，蓝牙模块的数据吞吐量 已经达到极限，会发生误码、丢包、甚至蓝牙连接中断的现象。受硬件性能 所限，只能在传输一字节后加入至少 100us 的延时间隔，使蓝牙模块能够较 稳定地工作，最终展示时，需要采用串口替代蓝牙来加速传输速度。

### 7.2 模拟电路部分

模拟电路部分主要包括电源驱动模块和电机驱动模块问题，虽然通过查阅 技术手册和基于 WEBENCH 的仿真可以看到基本的电路，但是从电路原理

7 课题开发与调试中出现的问题分析 | 18

图到电路实际工作还有很远的距离。
首先是电路原理图的设计，通过查阅资料，我们发现实验室提供的 TPS54160 模块输出电流为 1.5A，设计的 5V 电源不能很好的驱动 FPGA （1A）和舵机（800mA 堵转）。因此我们设计 FPGA 和 PCB 上的其他元件 一路供电，舵机和其他外设一路供电。这种设计虽然降低了电路的负载，但 是显然不可避免地增加了电路的规模和后续布线，制版，焊接的压力。 我们将整个电路进行整合为一块 PCB，这样从最大程度上减少了可能 存在的飞线和不稳定的情况，然而过大体量的电路带来了布线，制版，焊接 的困难。使用 AD 模块制作 PCB 的过程中，首先遇到的问题是 AD 不能提 供我们需要的元件封装库，因此我们参照元件的技术手册自行设计了封装 图。其次，包括 74HC244 模块等模块以及电阻电容等存在贴片（包括 SOP， SSOP 封装）以及插接封装（包括 DIP 封装），经过无数次的布线尝试，我 们尽可能的选择插接件来降低后续布线，焊接的难度。
接下来的布线部分，首先遇到的问题是 AD 的自动布线完全无法胜任 如此大体量的布线工作，最开始我们根据体量希望能够采用双面板来降低布 线难度，然而实验室很难提供相关的加工工具。因此我们选择单面板布线， 并只能采用手动布线方式，整个布线过程浪费了整整一周的时间。 布线中的另一个方面的困难是线宽的选择，一方面 TPS54160 不到 15mil 的引脚宽度要求布线最小宽度小于 15mil，另一方面 BTN 大电流 供电要求布线宽度尽可能宽，经过一系列的调整和选择，我们确定了适合负 载电流的布线宽度，保证每一条支路的电流不过载。然而，10mil 的线宽虽 然满足了大部分的需求，却对后续打孔，焊接的技术难度带来了巨大的麻 烦。另外，开始布线时部分地方布线过密，导致出现了 VCC，GND 之间距 离过小的问题，之后的 PCB 对这些部分尽可能的进行了调整。
之后是 PCB 的印制工作，在小学期开始前，我们曾请教过助教有关大 体量密集 PCB 雕刻的问题，发现抵达了雕刻机的上限，之后学期内具体采 用的是转印-腐蚀方式，然而这种方式对于技术水平仍有一定的要求，一方 面，版面过大导致散热过快，转印不能顺利实现，因此采取的解决方式是采 用多次转印的方式确保转印实现。另一方面，我们发现转印过程中由于线宽 问题也可能导致一些线出现中断等问题，具体的解决方式是采用 mark 笔进 行添加等，并对 PCB 的连接情况进行了细致的检查。 之后的钻孔和焊接方面也遇到了相当大的困难，一方面超过 200 个孔 使得钻孔体力消耗相当大，另一方面孔径过小，焊盘过小导致钻孔伤及焊 盘。这些问题我们通过自身的努力都已经尽可能的解决和避免了。焊接过 程中，首先遇到的问题是 SMT 的焊接工作。以 TPS54160 为例，其宽度为 3mm，一侧共有 5 个引脚，引脚宽度和引脚之间的间隙均不超过 20mil，不

7 课题开发与调试中出现的问题分析 | 19

仅如此，其下部还有一个散热引脚。初次焊接出现了巨大的问题，在助教的 帮助下完成了第一个芯片的焊接，然而后续的焊接也非常的吃力。这个问题 的解决方式是我们取李兆基大楼找电子工艺实习的师傅学习了一天的 SMT 焊接技术，并顺利完成了相关的焊接操作，使得该项技术达到了实用层次， 如图15是我们的最终成果。


Fig. 15: 手 焊 SMT 11 脚 芯 片
TPS54160 图

焊接技术的另一个问题是插接
件焊盘丢失的问题，一些插接件由
于打孔的问题出现了焊盘的不完整
等问题。具体的解决方式很大程度
上依靠了陈崴同学优秀的焊接技术，
同时，对于完成焊接的电路，进行逐
点测试短路并对短路部分予以隔断。
同时对可能存在的电流容量不足的
线路进行了上锡保证导电性。
电路组装完成后，仍然出现了大
量的问题，首先解决了大量的虚焊，
短路的问题。其次，为了固定摄像头
模块，我们在 PCB 上预留了相关位
置，然而由于原理图出现镜像对称问
题，摄像头前后两排引脚翻转，导致
摄像头被反向上电出现了一些损坏。
为了解决这个问题，我们不得不设计
另一个 PCB 将摄像头引脚反置，然
而，由于开始设计的过程中没有考虑
这方面的问题，导致新构建的 PCB 遮挡了一些排针和引脚，这个问题的解 决方法是我们另购了 L 形排针，将本来直插的排针改良为横接，基本上解 决了这个问题。
在电路实际运行的过程中，我们发现由于电机驱动力不足，我们不得不 提高 PWM 占空比来提升电机电流，然而，当电流过大时电源电压被拉低导 致后续电路失效供电失败，这个问题的解决方法是严格控制电机 PWM 占 空比，保证了电路可以正常运行。另外，我们进一步处理了电路接触不良的 问题，由于具体的问题和解决方法比较简单，这里省略。

8 项目创新点 | 20

### 8 项目创新点

### 8.1 摄像头的编写

目前市场上存在的图像传感器的封装各式各样，在选购外设时，我们综合考 虑了性能、成本、引脚数量、开发难度等因素，最终选择了 18 脚封装的带 有 FIFO 芯片的 ov7670 摄像头。这款外设由于封装较浅，所以价格也比较 低（约 70 元），在满足性能要求的前提下引脚数目也相对较少。虽然该摄像 头在硬件层面很接近底层，开发难度比其他深封装、外部接口简单、甚至自 身带有 MCU 的传感器要高出许多，但预计不会超出能力所及。在开发时也 对比了 FPGA 和单片机，虽然单片机使用高级语言编写代码，逻辑控制会 简单不少，但普通单片机的晶振频率要比 FPGA 低，IO 速度也比较慢，如 果还需要与 FPGA 进行通信则更加麻烦。因此最终选择使用 FPGA 来进 行开发，既能与其他模块更好地整合，又避免了与单片机通信造成的资源浪 费。

### 8.2 上位机的编写

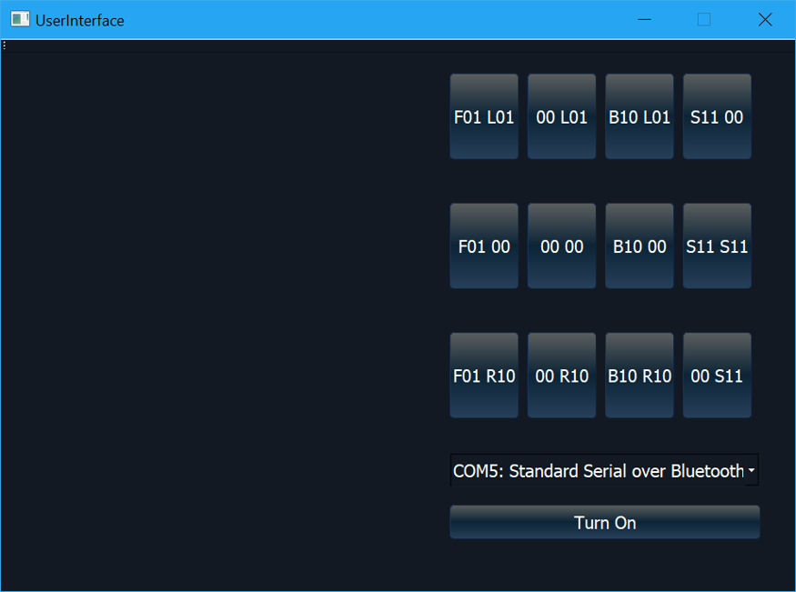
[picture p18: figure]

Fig. 16: 上位机的用户界面

我们采用 C++/Qt 编写了自己的上
位机程序负责遥控，图像解算，图像
显示和图像存储。相比其他小组采用
的手机端下载的成型 APP，我们自
行开发的程序可定制性更强，效率更
高。同时，不论采用串口和蓝牙，回
传的数据量解算都是相当大的，采用
现成的程序根本无法完成相关任务。
我们通过不断的调试，采用了多线程
技术来采集，解算，显示图像，保证
了上位机工作的稳定性和效率，保证
上位机不成为整个项目的瓶颈。
同时我们编写了精美的用户界面，方便用户通过键盘和鼠标进行控制 小车的速度。整个上位机的工作量甚至在一定程度上超过了 C++ 小学期同 类型大作业的工作量，并涉及到大量的 API，如蓝牙，串口，以及 openGL 等软件工程技术，提高了我们的软件能力以及软件和硬件交互能力。上位机 的用户界面如图16所示。

9 工作日志 | 21

### 8.3 PCB 的处理

我们设计了一块整合的 PCB，包括三个开关电源，一个驱动电路和若干外 围电路。采用 TPS54160 电源模块，虽然极大的增大了开发的难度，但是提 高了电源的效率，比起线性电源不到 50%，甚至更低，仅为 30% 的效率，我 们的理论效率可以达到 84%。同时，通过将 PCB 的整合，我们尽可能的避 免了飞线等情况，提升了电路的稳定性。整个 PCB 的难度和体量均为整个 课程组里最大的之一。

### 9 工作日志

简要的工作日志如表5所示，由于我们采用了免费、开源的分布式版本控制 系统 Git，并将所有代码托管在面向开源及私有软件项目的托管平台 (https://github.com/ZeroWeight/Project-of-Electronic-Circuits) Github 中，我们可以很简单的管理我们的工程以及检查我们的进度，同时有效加速 团队间的协作进度以及防止可能存在的错误修改，提高开发效率。详细的工 作日志如附加文件所示。详细的工作日志请参阅提交记录 (https://github.com/ZeroWeight/Project-of-Electronic-Circuits/commits/master)

### 10 项目总结和感想

经过两周的努力以及之前的一些铺垫，我们完成了整个项目从规划设计到 具体实现的各种环节，有了比较大的收获。
首先是项目的规划，跟进方面。在项目规划过程中，我们在 7 月份就 提出了一份明确的规划方案，之后的工作均按照方案实行。在合作方面，我 们队友之间配合紧密，合理的采用了 Github 等团队合作，代码托管工具加 速了我们的合作进程。技术水平的相近保证了我们团队分工均匀有效，每个 人都可以发挥自己的特长。模块分工清晰明确，陈崴同学负责了几乎所有 的 Verilog 代码的实现，而张蔚桐负责了所有的上位机实现和模拟电路部分。 这种分工方式使得我们不论是合并工作量还是检查错误都有着明确的方向， 也不会发生队友之间相互“甩锅”的情况。
其次是对于硬件软件电路的关系的理解，通过这个项目我们了解到，虽 然相比于模拟电路，数字电路的稳定性和可展示性更强；相比于硬件底层的 封装，同样工作量的软件工程，或者是顶层的综合更加“出彩”，但是模拟 电路，底层封装的重要性是不可忽视的。底层电路是整个项目的基础，更好 的了解底层的情况有助于我们对顶层进行更好的封装。例如，我们采用的摄 像头模块是 18 引脚的底层封装，相比于其他组用的高级摄像头模块，带来 了大量的工作量，然而，我们的摄像头造价更低，不考虑其他硬件瓶颈限制， 我们的摄像头采集速度也更快，采集方式也更灵活。

10 项目总结和感想 | 22

Tab. 5: 工作日志表
小学 期之 前 | 主要完成了蓝牙模块，摄像头模块，上位机，电路原理图 和 PCB 布线的分模块的工作，并分模块进行了检验，其 中上位机顺带完成了一个上位机自检测试程序。基于 WEBENCH 完成了电源模块的设计，并综合了电机驱动 到一块 PCB 上，完成了复杂的布线工作，为小学期做好 了相关的准备
工作 日 周 | 周一 | 周二 | 周三 | 周四 | 周五
| 上 午 | 综合了假 期的工作 进度，摄 像头模块 和上位机 模块进行 了联调 | PCB 版 印刷完 毕，检查 相关问题 以及准备 打孔工作 | 审查 PCB 发 现 PCB 出现印刷 质量问 题，发回 实验室重 新制作 | 赴李兆基 大楼完成 SMT 以 及绝大部 分插接件 的焊接工 作 | 修正 PCB 问 题和错 误，整车 组装空载 测试
| 下 午 | PCB 原 理图交付 实验室印 刷，上位 机模块发 布稳定版 本提供后 续使用 | PCB 打 孔，焊接 工作（包 括 SMT 焊接以及 插接件焊 接） | 赴李兆基 大楼进行 PCB 打 孔，刷松 香以及学 习 SMT 相关焊接 技术并进 行练习 | 完成 PCB 的 焊接工 作，检查 PCB 电 路的工作 性能并进 行调整 | 赴中发电 子市场购 买其他电 子元件， 并为实验 室提供相 关电子元 件
第 二 周 | 上 午 | 完成基于 Lab-VIEW (myRIO) 的陀螺仪 配置 | 小车落地 遥控，检 查通信协 议，准备 验收 | 验收 | 视频录 制，器件 归还 | 展示工作
| 下 午 | 设计完成 红外测速 功能 | 修正电 路，检查 蓝牙速度 上线，寻 找代替蓝 牙信道的 替代方 式，通报 验收 | 休整，准 备项目结 题 | 制作展示 PPT，器 件归还 | – –

第
一
周

11 项目完成情况 | 23

这次课程设计，我们从底层硬件电路层面到上位机纯软件层面进行了 设计，实现了一个从硬件到软件有机整合的项目，也得到了相比于之前做的 软件项目不同的进步。通过和硬件层面的了解，我们了解到一些事实存在的 行业瓶颈，了解到了软硬件结合的过程中硬件电路的重要性。通过实际硬件 电路的了解，设计，制作这些过程，我们增长了硬件电路调试设计的很多经 验，如 PCB 设计的合理性等，方便了我们之后进一步的硬件项目的设计。 最后的最后，我们发现尤其是对硬件部分，性能上的需求是远远高于实 际的实现的，本次设计过程的过程中我们克服了大量的硬件瓶颈问题，例如 蓝牙模块，上位机速度问题。生产更高速，更小型化，更稳定的硬件模块， 例如研发更高速的无线通信方式，如目前正在逐步推进的 5G 网络等，永远 是硬件领域的核心的，最意义的发展方向，也希望我们之后能够在此领域内 做出自己的微小的贡献！

### 11 项目完成情况

项目完成情况良好，小车模型如下图所示。蓝牙图像回传收到前面提到的数 据量和速度的问题受限，采用串口代替蓝牙可以得到比较好的图像，一些图 像如下页所示，作品视频可以参考视频文件


Fig. 17: 小车最终模型

11 项目完成情况 | 24

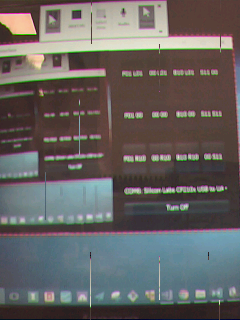
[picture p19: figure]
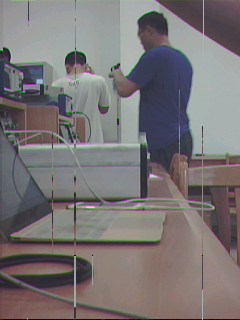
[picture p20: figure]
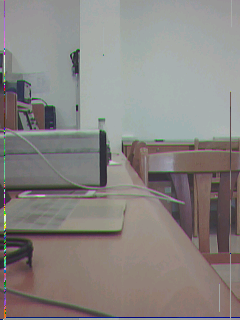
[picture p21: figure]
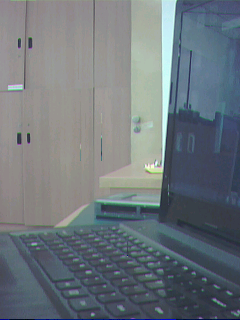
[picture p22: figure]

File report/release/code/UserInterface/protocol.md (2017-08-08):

# 通信协议

```verilog
8'b 11 xx yy 00
```
- `xx` `yy`间无相互作用 
- 一旦丢包，认为执行上个有效包的动作

## xx

```verilog
2'b00 : 停止（无动作）
2'b01 : 前进（以一个恒定速度或者越来越快）
2'b10 : 后退，同上
2'b11 : 刹车
```

## yy

```verilog
2'b00 : 无动作，保持舵机角度不变
2'b01 : 左转，舵机逆时针旋转（驱动PWM占空比变大）
2'b10 : 右转，舵机顺时针旋转（驱动PWM占空比变小）
2'b11 : 舵机复位，归为正常位置
```

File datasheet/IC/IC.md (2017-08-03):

# 需要采购的IC
[74HC244D * 1](https://detail.tmall.com/item.htm?id=12825812454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)

[BTN7971B * 2](https://detail.tmall.com/item.htm?id=39989151852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)

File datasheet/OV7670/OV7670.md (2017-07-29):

# 不含FIFO的OV7670
## OV7670管脚封装
|外管脚|内管脚|管脚名|IO|作用|
|----|----|----|----|----|
|3|3|SIO_C|I|SCCB CLK INPUT|
|4|2|SIO_D|IO|SCCB DATA INPUT|
|5|13|VSYNC|O|帧输出标志|
|6|14|HREF|O|行输出标志|
|7|15|PCLK|O|Pixel CLK Output|
|8|17|XCLK|I|System CLK Output|
|9~16|***|D[7:0]|O|YUV/RGB Output|
|17|21|RESET|I|低电平重置|
|18|6|PWDN|I|高电平省电模式|

## 配置
- 供电要求：3V3，10mA
- XCLK：24MHz时钟，占空比50%
- SCCB时钟要求：不超过400Hz，低电平不少于1.3us，高电平不少于0.6us
- 简单起见，传输信号保持时间，空闲时间均多于2us，包括
    - 建立新传输
    - 电平维持时间
- 输出：PCLK 5ns之后信号稳定

## 输出方式（以640*480输出为例）
```verilog
always @ (posedge vsync);下降沿也可
prepare <= ~prepare
;vsync第一个上升沿准备，第二个上升沿放弃准备

always @(posedge pclk)
begin
if (prepare & href);href 高电平480次
;data readin and move to next pixel;一行640个
end
```
## SBBC 驱动  
### 开始传输  
```C
SIO_C = 1;
SIO_D = 1;
delay_ns(1250);
SIO_D = 0;
SIO_C =0;从下一个SIO_C的上升沿读取
```
### 结束传输
```
SIO_C = 1;(在9b传输完成之后，本次上升沿不读取)
SIO_D = 1;
delay_ns(50);
SIO_D = 0;
```
### 写
SIO_C 上升沿读取数据
9b：dont care bit主机不管此数据，仅空转时钟
写3B
- ID[7:1] +0(写) 8`h42
- 地址
- 值

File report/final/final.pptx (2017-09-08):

## 基于受控车的场地探测系统

电子设计小学期
终结报告
张蔚桐 2015011493
陈 崴 2015011481

## 项目背景

- 在小车上加装图像传感器和其他场地检测装置，采集环境信息
- 方便人员远程控制，可进入危险场合作业
- 采集到的信息可以进一步处理

## 数电部分

顶层控制
异步时钟
电机控制
舵机控制
通用异步收发器
CMOS图像传感器
超声波测距
初始化寄存器
FIFO
采集图像
读取图像
串口发送
串口接收

## 通用异步收发器

- 串口发送
  - 电平触发信号，开始发送
  - 发送完成后产生应答信号
- 串口接收
  - 起始位（低电平）触发
  - 接收完成或接收错误产生应答信号
  - 改进：采样降低误码率

## CMOS图像传感器

- 初始化寄存器
  - SCCB协议

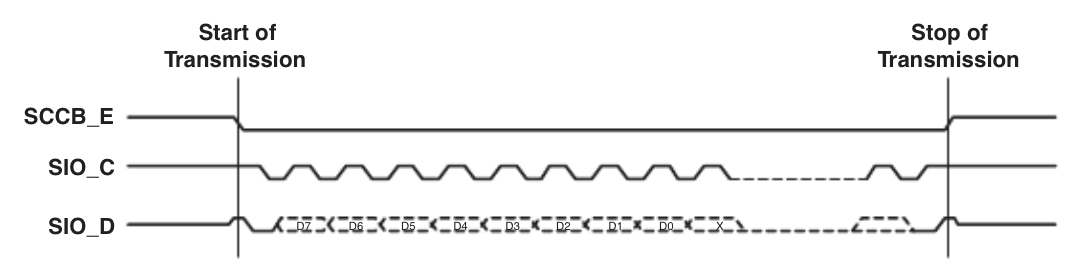
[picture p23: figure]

## CMOS图像传感器

- 初始化寄存器
  - SCCB协议

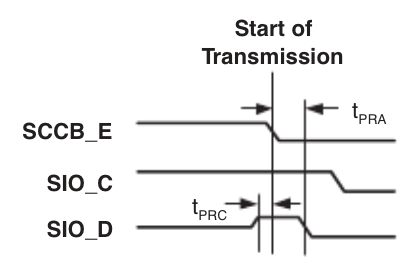
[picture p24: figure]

## CMOS图像传感器

- FIFO
  - 采集图像


## CMOS图像传感器

- FIFO
  - 读取图像


## 调试中出现的问题

- HC-05主从一体蓝牙串口模块
- 波特率921600 ≈ 11µs per byte ≈ 3.3s per QVGA frame
- 波特率不影响RFCOMM实际数据吞吐量
- 数据吞吐量过大时传输不稳定

## 模拟电子电路部分

- 基于WEBENCH的原理图仿真
  - 使用实验室提供的TI芯片TPS54160作为开关电源模块并直接使用，理论效率高达84%
  - 问题：WEBENCH集成度太高，带来后续芯片焊接难度大
  - 创新点：在WEBENCH提供的电路图基础上，适当调整了电阻电容的取值，降低了电路成本


## 模拟电子电路部分

- 电路原理图和PCB的绘制
  - 驱动芯片使用BTS7971半H桥电路，接受PWM调制
  - 创新点：所有功能集成到一块PCB，方便后续工作，包括摄像头的插接等。PCB体量大，布线难度大
  - 问题：电路集成化过高导致焊接部分出现困难


## 模拟电子电路部分

- PCB的印制和焊接工作
  - 难点
    - SMT焊接技术
    - 插接件焊盘较小，钻孔易伤及焊盘
    - 线宽较小，不论是腐蚀还是雕刻难度大
  - 向李兆基电子工艺实习师傅学习了SMT的焊接技术，并达到实用水平
  - 陈崴同学插接件焊接技术一流，保证了电路稳定运行


## 模拟电子电路部分

- 后续电路调整和维护
  - 大功率负载检测电源工作性能通过
  - 修复了一些由于焊接缺陷、元件缺陷的电路问题
  - 问题
    - 电机占空比过高并出现堵转时电源电压拉低导致开关电源无法输出需要的电压
    - 发现电机驱动效率较低，相比别组的车而言速度极慢
    - 解决方式：确定合适的输出占空比


## 附加工作

- 完成了蓝牙+解算图像+显示图像+存储图像的上位机模块
  - 采用C++/Qt，使用多线程处理大量数据吞吐量
  - 并顺便完成了上位机的自检测程序
  - 合计C++代码600行左右（竟然差不多赶上了C++小学期代码ORZ）


## 项目展望

- 上位机部署到移动平台，实现移动控制
  - 难点：上位机计算性能要求高，移动平台需要进一步处理
- 利用回传图像进行3D建模
  - 不使用位置信息进行建模
  - 使用位置信息进行建模的研究，试图增加建模精度
- 使用WIFI模块取代蓝牙模块实现实时通信
  - 难点：引脚多，TCP/IP协议复杂

## 开发流程


## 谢谢大家，请批评指正

电子设计小学期
终结报告
张蔚桐 2015011493
陈 崴 2015011481

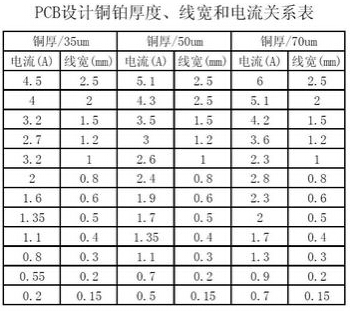
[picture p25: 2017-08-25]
report/preview/pcb.jpg

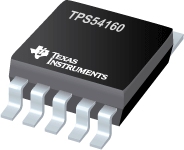
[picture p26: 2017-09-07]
report/final/TPS54160.jpg

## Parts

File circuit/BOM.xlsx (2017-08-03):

 | 3.3V |  |  |  | 5V |  |  |  | Type | Val.@footprint | Num | Website
Name | Min. Val. | Typ. Val. | Max. Val. | Val.@footprint | Min. Val. | Typ. Val. | Max. Val. | Val.@footprint | C | 3.3n@0805 | 3 | C (https://detail.tmall.com/item.htm?id=15680792156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)
RenT | 103.4k | 103.4k | 124.1k | 110k@0805 | 103.4k | 103.4k | 124.1k | 110k@0805 | C | 4.7n@0805 | 3
RenB | 12.45k | 12.45k | 14.94k | 11k@0805 | 12.45k | 12.45k | 14.94k | 11k@0805 | C | 100n@0805 | 2
Ccomp2 | 4.076p | 40.76p | 203.8p | 47p@0805 | 379.4f | 3.794p | 18.97p | 4.7p@0805 | C | 47p@0805 | 1
Rcomp | 15k | 150k | 150k | 150k@0805 | 15k | 150k | 150k | 150k@0805 | C | 4.7p@0805 | 1
Ccomp | 330.4p | 3.304n | 16.52n | 3.3n@0805 | 503.4p | 5.034n | 25.17n | 4.7n@0805 | C | 1n@0805 | 1
Css | 5.625n | 6.25n | 6.875n | (1n,2.2n,3.3n)@0805 | 5.625n | 6.25n | 6.875n | (1n,2.2n,3.3n)@0805 | C | 2.2@0805 | 1
Rt | 1.369M | 1.369M | 1.643M | 1.5M@0805 | 1.369M | 1.369M | 1.643M | 1.5M@0805 | C | 10V470u@6*12 | 2 | C_e (https://detail.tmall.com/item.htm?id=13578847100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)
Cin | 2.792u | 2.792u | 100u | 4.7u@0805 | 4.23u | 4.23u | 100u | 4.7u@0805 | D | ss24@sma | 2 | SS24 (https://detail.tmall.com/item.htm?id=41154125912&rn=73b954e50fd325eed47c489a9584b9fd&abbucket=0)
Cboot | 100n | 100n | 100n | 100n@0805 | 100n | 100n | 100n | 100n@0805 | L | 100u@0805 | 2 | L (https://detail.tmall.com/item.htm?id=16984466294&rn=219290933fcf17c34fd9b4064001c39b&abbucket=0)
L1 | 57.25u | 57.25u | 171.7u | 100u@0805 | 74.13u | 74.13u | 222.4u | 100u@0805 | R | 1k@0805 | 8 | R (https://detail.tmall.com/item.htm?id=13516815072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)
D1 | 0.55V@2A |  |  | ss24@sma | 0.55V@2A |  |  | ss24@sma | R | 110k@0805 | 2
Rfbt | 31.25k | 31.25k | 34.37k | 33k@0805 | 52.5k | 52.5k | 57.75k | 56k@0805 | R | 11k@0805 | 2
Rfbb | 10k | 10k | 10k | 10k@0805 | 10k | 10k | 10k | 10k@0805 | R | 150k@0805 | 2
Cout | 303.3u | 303.3u | 1.516m | 10V470u@6*12 | 200.2u | 200.2u | 1.001m | 10V470u@6*12 | R | 10k@0805 | 2
非Risym |  |  |  |  | 电子元件配单 订单 电子元器件 IC芯片二三极管电容电阻 差价补拍 |  |  |  | R | 33k@0805 | 1
BTN7971B (https://detail.tmall.com/item.htm?id=39989151852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) |  | （淘宝） |  |  |  |  |  |  | R | 56k@0805 | 1
TPS54160 (https://detail.tmall.com/item.htm?id=44016025819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) |  | （学校） |  |  |  |  |  |  | R | 1.5M@0805 | 1 | MR (https://detail.tmall.com/item.htm?id=13675195853)
 |  |  |  |  |  |  |  |  | IC | 74HC244D@SOP20 | 1 | 74HC244 (https://detail.tmall.com/item.htm?id=12825812454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)

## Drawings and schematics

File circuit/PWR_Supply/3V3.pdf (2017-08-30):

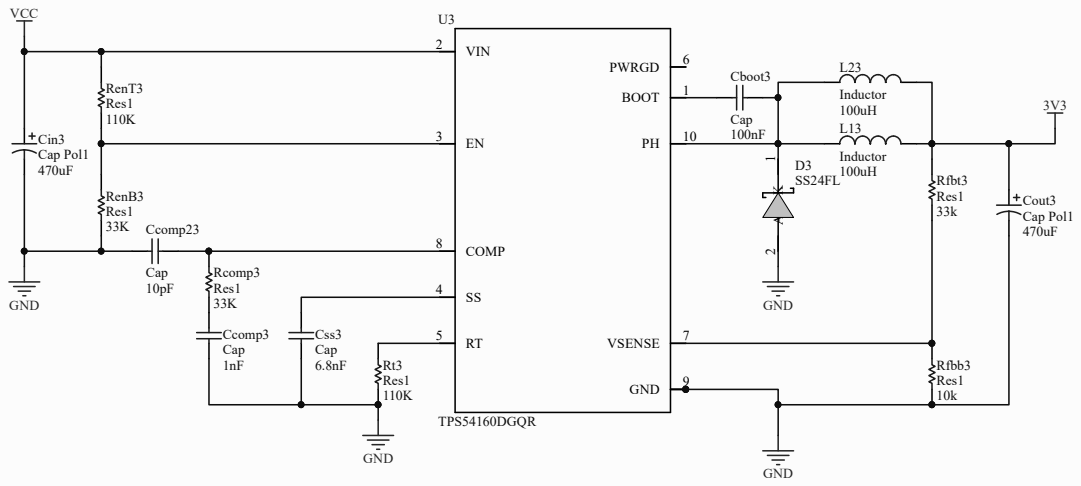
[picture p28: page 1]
Title; Size; Number; Revision; Date:; Sheet of; File:; C:\Users\..\3V3.SchDoc; Drawn By:; Cin3 Cap Pol1; RenT3 Res1; RenB3 Res1; Rcomp3 Res1; Rt3 Res1; Ccomp23; Cap; Ccomp3 Cap; Css3 Cap; BOOT; VIN 2; PWRGD; VSENSE; COMP 8; GND; TPS54160DGQR; VCC; Cboot3; Inductor; Rfbt3 Res1; Rfbb3 Res1; Cout3 Cap Pol1

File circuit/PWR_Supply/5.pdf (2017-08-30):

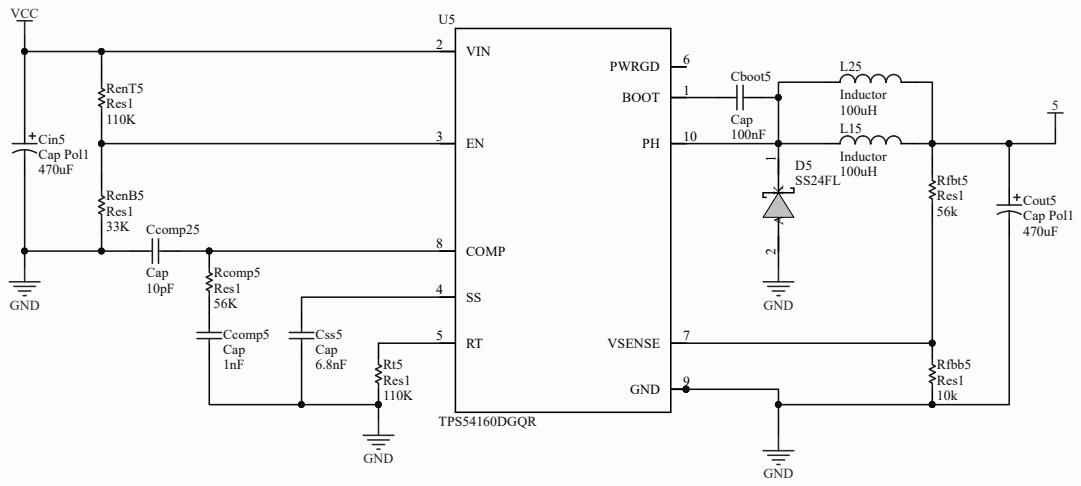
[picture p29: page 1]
Title; Size; Number; Revision; Date:; Sheet of; File:; C:\Users\..\5.SchDoc; Drawn By:; Cin5 Cap Pol1; RenT5 Res1; RenB5 Res1; Rcomp5 Res1; Rt5 Res1; Ccomp25; Cap; Ccomp5 Cap; Css5 Cap; BOOT; VIN 2; PWRGD; VSENSE; COMP 8; GND; TPS54160DGQR; VCC; Cboot5; Inductor; Rfbt5 Res1; Rfbb5 Res1; Cout5 Cap Pol1

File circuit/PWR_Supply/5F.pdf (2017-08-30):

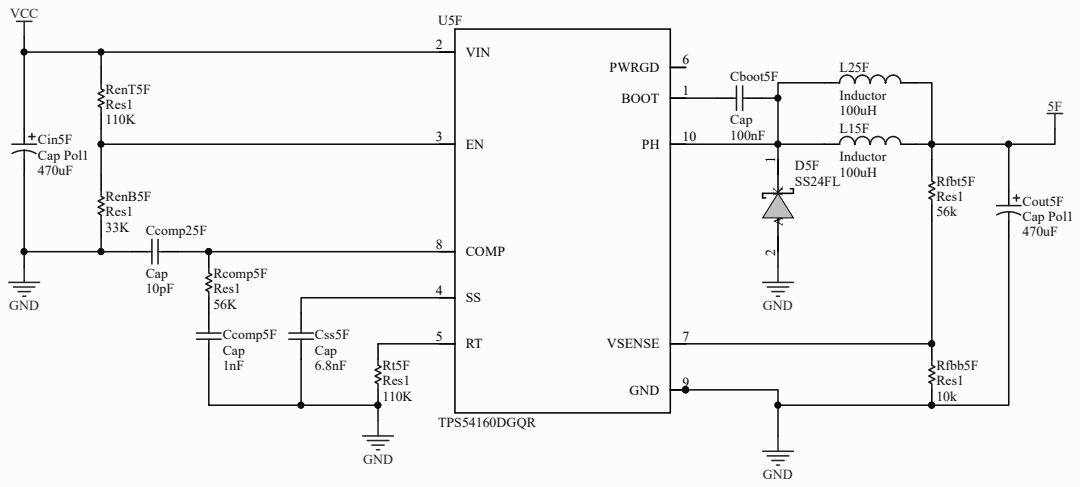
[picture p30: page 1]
Title; Size; Number; Revision; Date:; Sheet of; File:; C:\Users\..\5F.SchDoc; Drawn By:; Cin5F Cap Pol1; RenT5F Res1; RenB5F Res1; Rcomp5F Res1; Rt5F Res1; Ccomp25F; Cap; Ccomp5F Cap; Css5F Cap; BOOT; VIN 2; PWRGD; VSENSE; COMP 8; GND; TPS54160DGQR; VCC; Cboot5F; Inductor; Rfbt5F Res1; Rfbb5F Res1; Cout5F Cap Pol1

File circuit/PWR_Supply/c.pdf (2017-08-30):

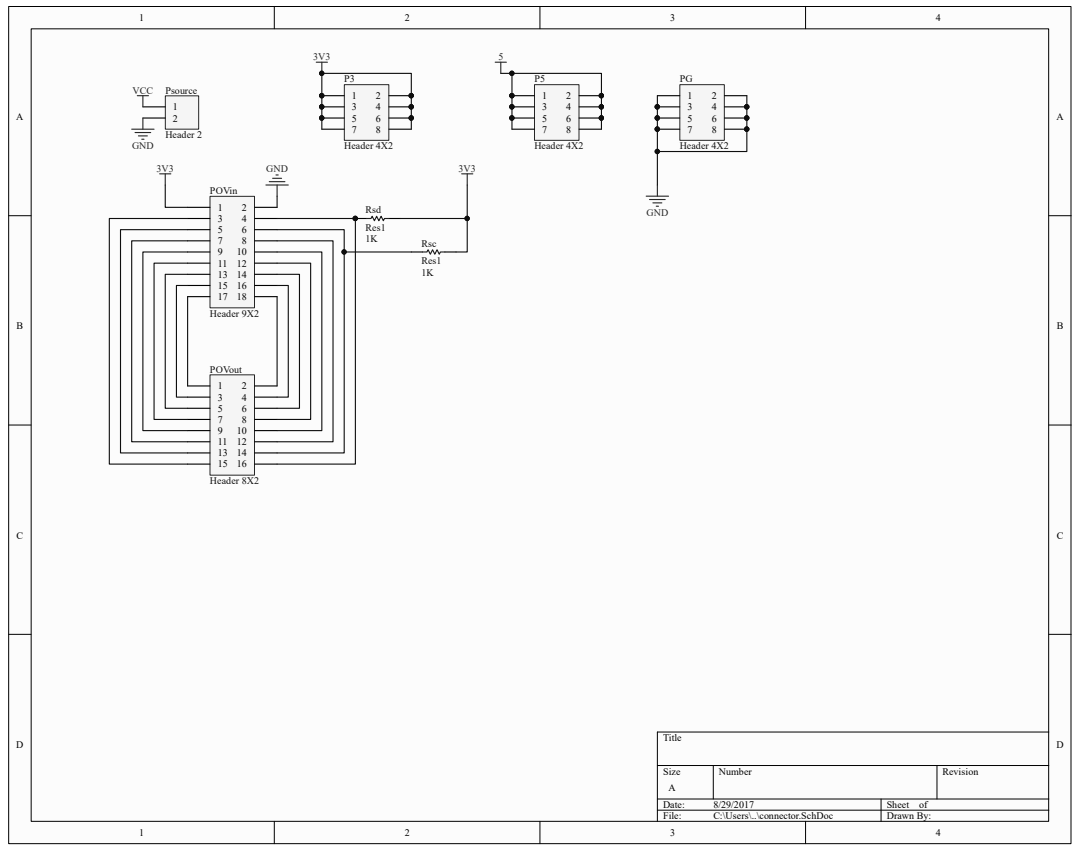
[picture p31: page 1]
Title; Size; Number; Revision; Date:; Sheet of; File:; C:\Users\..\connector.SchDoc; Drawn By:; Psource; Header 2; GND; VCC; POVin; Header 9X2; POVout; Header 8X2; Header 4X2; Rsd; Res1; Rsc

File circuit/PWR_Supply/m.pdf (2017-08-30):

# A7 17 GND 10 VCC ²⁰

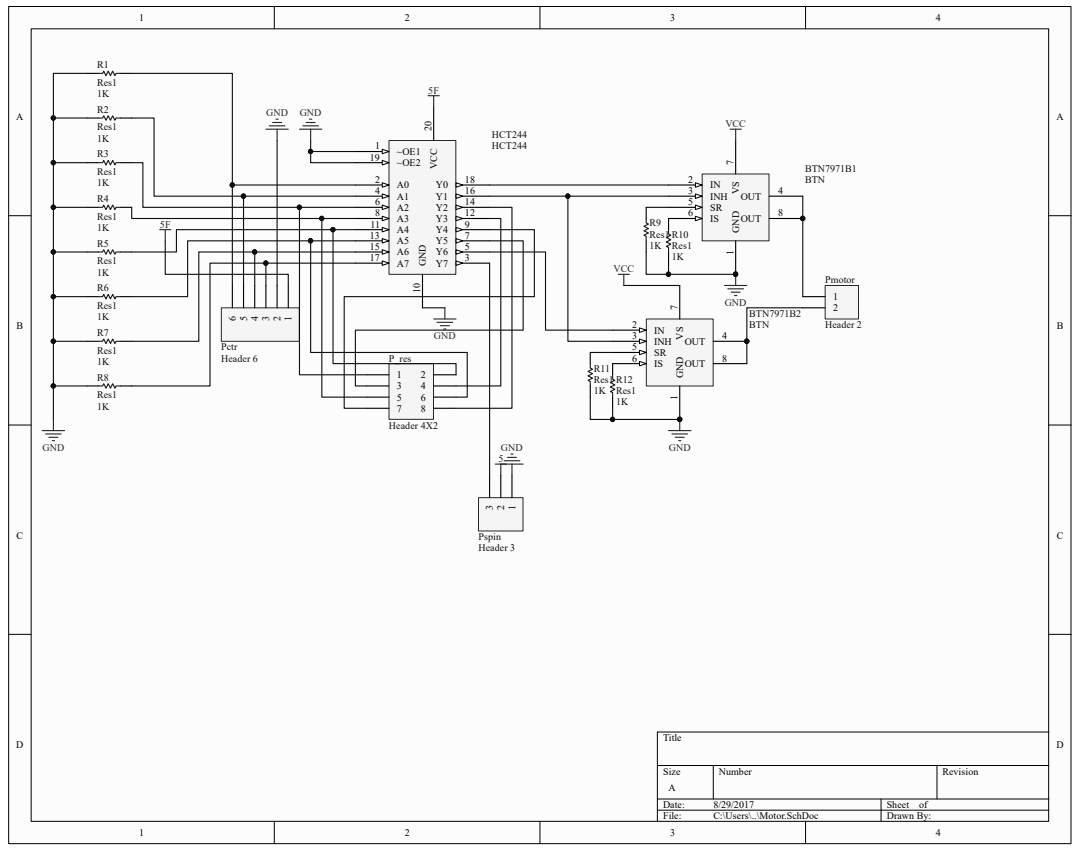
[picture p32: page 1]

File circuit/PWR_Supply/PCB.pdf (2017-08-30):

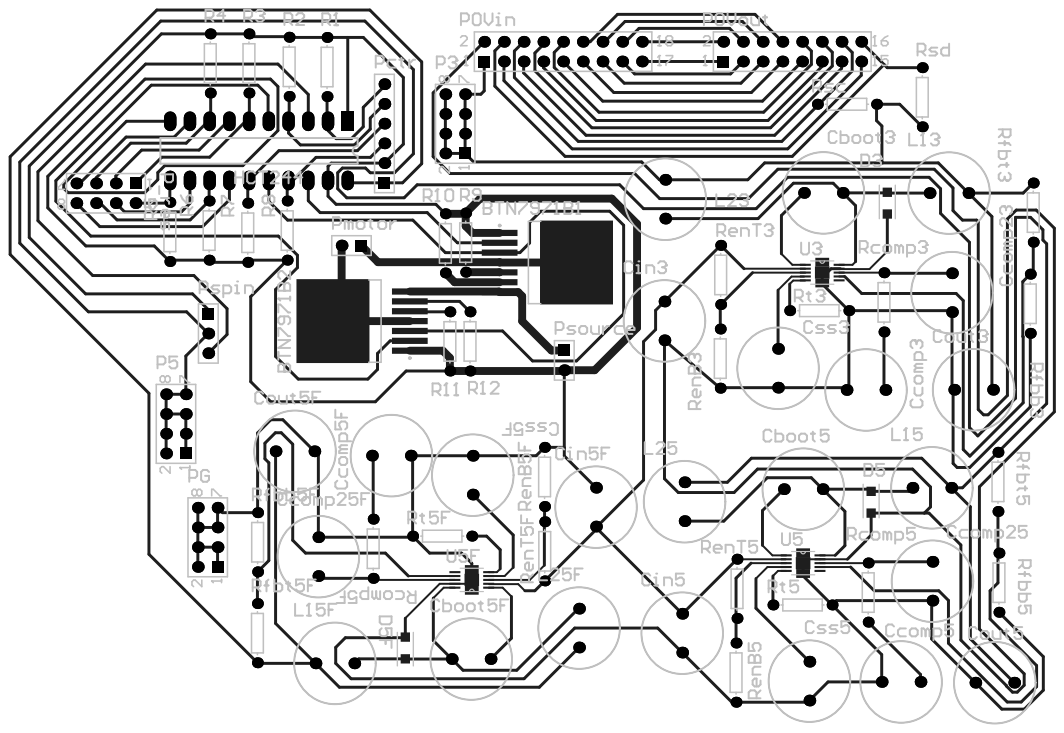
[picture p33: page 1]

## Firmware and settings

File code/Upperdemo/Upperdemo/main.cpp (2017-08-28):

#include <QtCore/QCoreApplication>
#include <QSerialPort>
#include <QString>
#include <QObject>
#include <QTimer>
#include <opencv2/core.hpp>
#include <opencv2/highgui.hpp>
#include <opencv2/imgproc/imgproc.hpp>
#include <iostream>
int main (int argc, char *argv[]) {
	QCoreApplication a (argc, argv);
	QSerialPort sp;
	QTimer timer;
	timer.setInterval (0);
	sp.setPortName ("COM2");
	sp.setBaudRate (115200 * 8);
	sp.setFlowControl (QSerialPort::NoFlowControl);
	sp.setDataBits (static_cast<QSerialPort::DataBits>(8));
	sp.setStopBits (QSerialPort::OneStop);
	sp.setParity (QSerialPort::NoParity);
	sp.open (QSerialPort::ReadWrite);
	cv::VideoCapture capture;
	capture.open ("vip_car.avi");
	cv::Mat frame;
	cv::Mat des (240, 320, CV_8UC3);
	QByteArray arr[100][240];
	int f = 0;
	for (int i = 0; i < 100; ++i)for (int j = 0; j < 240; ++j)
		arr[i][j].resize (320 * 2 + 2);
	while (1) {
		capture >> frame;
		if (frame.empty ()) break;
		cv::resize (frame, des, des.size (), (0, 0), (0, 0), cv::INTER_CUBIC);
		for (int i = 0; i < 240; ++i) {
			for (int j = 0; j < 320; ++j) {
				uchar B = des.at<cv::Vec3b> (i, j)[0];
				uchar G = des.at<cv::Vec3b> (i, j)[1];
				uchar R = des.at<cv::Vec3b> (i, j)[2];
				arr[f][i][j * 2] = (R & 0xF8) | (G >> 5);
				arr[f][i][j * 2 + 1] = ((G & 0xFC) << 3) | (B >> 3);
			}
			arr[f][i][640] = 0x0D;
			arr[f][i][641] = 0x0A;
		}

		cv::imshow ("Example2", des);
		cvWaitKey (30);
		++f;
	}
	int i = f = 0;
	QObject::connect (&timer, &QTimer::timeout, [&](void) {
		if (i == 239) {
			sp.write (arr[f][i], 642);
			i = 0;
			++f;
		}
		else {
			sp.write (arr[f][i], 640);
			++i;
		}
		if (f == 100) timer.stop ();
	});
	timer.start ();
	return a.exec ();
}

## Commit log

2017-07-30 [A] PCB lib for AD add in,
    [PCB.PcbDoc, PWR_Supply.PrjPcb, Sheet.SchDoc]
2017-07-30 [F] 3v3 sch finished
    [PCB.PcbDoc, PWR_Supply.PrjPcb, Sheet.SchDoc]
2017-07-31 [A] user interface
    [PcbLib.PcbLib, Schlib1.SchLib]
2017-07-31 [A] uart modules Verilog串口模块，波特率可调，8数据位，无校验位，1停止位。 高波特率时有误码现象，需改进。
2017-07-31 [A] uart modules
2017-08-01 [D] remove useless project in circuit/
2017-08-01 [A] read frame data (untested)
2017-08-01 [A] rtl top (untested) 整合了摄像头初始化、数据读取和串口通信。 帧数据按每像素先高字节后低字节的顺序发送至上位机，每帧以0x0D 0x0A结束，共320 × 240 × 2 + 2 = 153602字节。
2017-08-02 [A] Bill Of Materials
    [BOM.xlsx]
2017-08-02 [U] read frame data (simply tested) - 摄像头只可初始化一次，若初始化中断或错误或重新初始化，则需要重新上电。所以注释了OV_INIT.v LINE51。 - （未测试）目前只处理了QVGA的一帧，即只使用FIFO的一半空间。 - 目前发给上位机的数据中，前328B为初始化返回值，若初始化成功，则第7字节为0x73，第11字节为0x76，第327字节为0x0D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
2017-08-03 [U] output to file, BUG: cant exit normally
    [main.cpp]
2017-08-03 [bug fixed] - fix the bug of exit - refine the method to write to files - can accept 10ms/640B input - may rely on the performance of computer - NOT stable
    [main.cpp]
2017-08-03 [A] resource of PCB all finished
    [PCB.PcbDoc, PWR_Supply.PrjPcb, PcbLib.PcbLib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]
2017-08-03 [U] update the BOM
    [BOM.xlsx]
2017-08-04 [U] ov7670 generally works :bangbang: :large_blue_circle: 修改了一下初始化配置，不一定比原来好，可以进一步测试。现在初始化返回值共517字节。 :large_blue_circle: 初始化后的几帧可能不太稳定，直接舍弃。 :large_blue_circle: 读取图像速度改为100us每字节，需在上位机方面优化。 :red_circl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
2017-08-04 [U] a temp commit with lots of bugs to be fixed
    [main.cpp]
2017-08-05 [U]IMPORTANT UPDATE: fix bugs of host
    [main.cpp]
2017-08-06 [A] simply finish the PCB design
    [PWR_Supply.PrjPcb, Sheet.SchDoc]
2017-08-06 [U] update pins for OV
    [PCB.PcbDoc, PWR_Supply.PrjPcb, Sheet.SchDoc]
2017-08-07 [A] finish the PCB
    [PCB.PcbDoc, PCB1.CSV, PCB1.PcbDoc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]
2017-08-08 [U] protocol - servo
2017-08-08 [A] servo
2017-08-08 [U] servo
2017-08-10 [D] remove uesless PCB component
    [PCB.PcbDoc, PCB1.CSV]
2017-08-23 [U] finish PCB
    [PCB.PcbDoc, PCB1.CSV, PCB1.PcbDoc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]
2017-08-24 [U] release PCB
    [PCB.PcbDoc, PWR_Supply.PrjPcb]
2017-08-25 [U] report finish part 1 and 2
    [PCB.PcbDoc]
2017-08-25 [U] README“
2017-08-28 [U] renew the host machine coder
    [PWR_Supply.PrjPcb]
2017-08-28 [A] motor module
2017-08-31 [U] myRIO project resources
    [PWR_Supply.PrjPcb, addon.PcbDoc]
2017-09-04 [U] servo and motor pwm
2017-09-05 [A] ultrasonic ranging module
2017-09-10 [U] creative point: image sensor
2017-09-10 release code
    [PCB.PcbDoc, PWR_Supply.PrjPCB, addon.PcbDoc]
